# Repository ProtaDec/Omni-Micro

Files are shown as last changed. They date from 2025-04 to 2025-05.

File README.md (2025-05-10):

# Omni-Micro
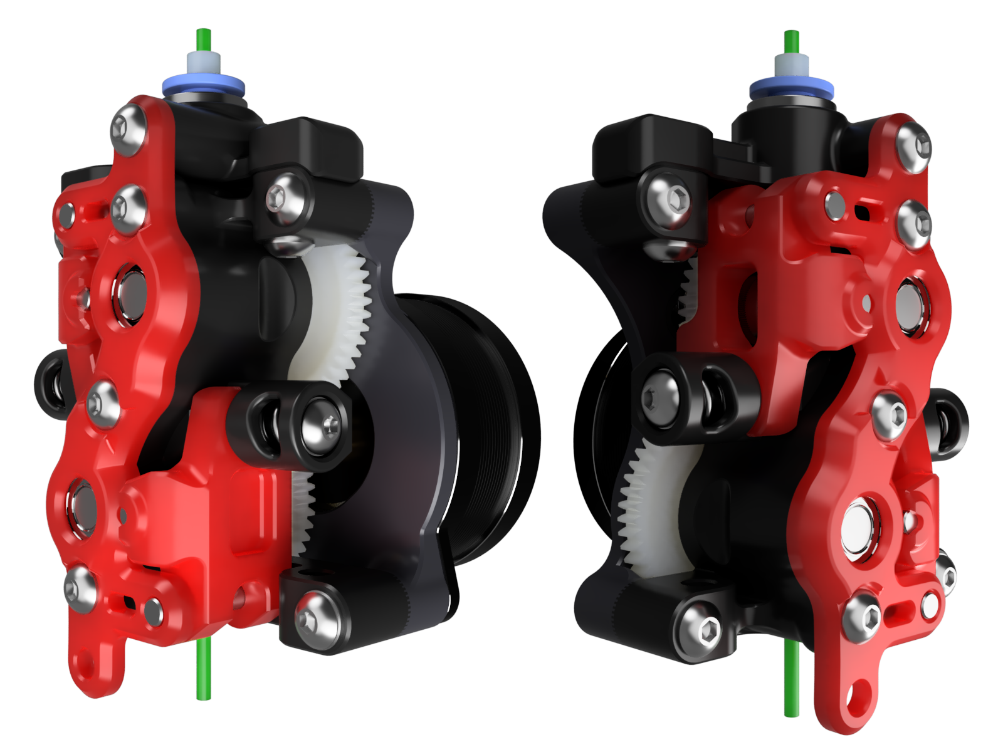
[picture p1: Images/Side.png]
My Image

Double grip modular extruder, based on [Sherpa Micro](https://github.com/Annex-Engineering/Sherpa_Micro-Extruder) by Annex Engineering.
## Concept Features
- Double grip extruders have existed for a while. They help conventional* hotends reach their thermal bottleneck, adding weight and build cost;
- Smooth idler extruders, on the other hand, have proved to increase extruson consistency at the loss of grip;
- I consider this extruder a spiritual successor of the [Sherpa Crew Mini](https://github.com/jrlomas/Sherpa-Crew-Mini) by KR, whom I've been in contact with for a while. I like to think I have improved on the existing formula, while they went for something entirely different, [Mirò](https://github.com/jrlomas/miro-extruder).
  
*Untested with new-generation hotends such as [Chube](https://chubehotend.com/) by Luke's Laboratory.
## Design-specific features
- No alteration of leftover original design elements, except for "fusing" two units;
- Flippable design, compatible with most sherpa micro-friendly toolheads (TBD);
- Four driving configurations & three bowden fitting options;
- Split tensioner with either two regular springs or one cut spring;
- First layer squish compensation built-in (reliability to be confirmed);
- Idler arms and tensioners are compatible with regular Sherpa Micro.
## Future Additions
- Filament sensor;  
  I have an idea of how I want to go about it, but I currently don't own any multi-material DIY printers, and the motivation just isn't there.
- Skeletonized Housing_Rear (maybe).
# BOM
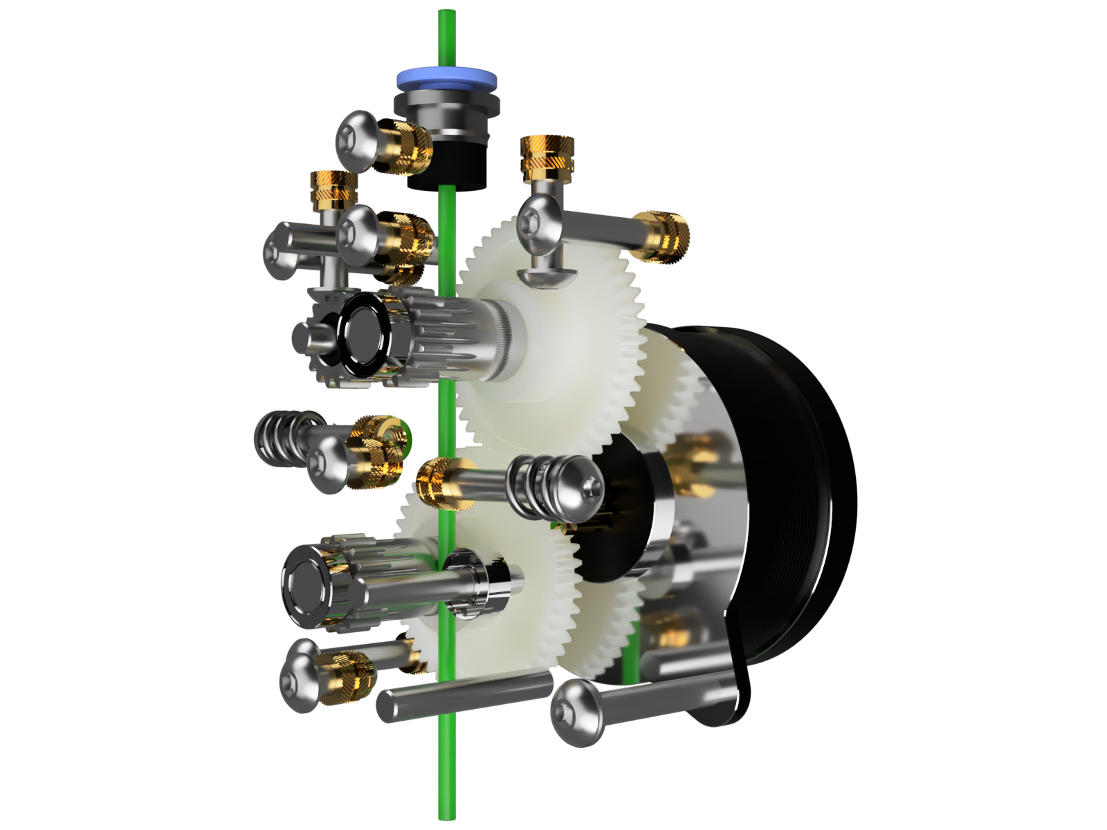
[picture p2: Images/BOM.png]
My Image

## Fasteners

| Article | Qty | Notes |
|---|---|---|
| M3x6(+)mm Ultra Low Profile | 1 | For motor |
| M3x6mm BHCS | 1÷2 | |
| M3x8mm BHCS | 2 | |
| M3x12mm BHCS | 0÷2 | Bowden cap  |
| M3x18mm BHCS | 5 | |
| M3x20(+)mm BHCS | 1 | For motor |
| 3x6x0.2mm Shim | 1 | For motor |
| 3x6x0.5mm Shim | 3 | |
| M3x5x4mm Heat-set Insert | 8÷11 | |

## Extruder Parts

| Article | Qty | Notes |
|---|---|---|
| NEMA14 36mm Stepper 10t to 6t | 1 | |
| BMG Driving Gear Assembly | 2 | OEM RIDGA V2 preferred |
| BMG Idler Gear Assembly | 1÷2 | |
| MR73 Ball bearing | 1÷2 | |
| M3x20 Idler pin | 2÷4 | may need sanding for mr73 |
| Bondtech Spring | 1÷2 | |
| E3D 5mm Collet | 0÷1 | |
| E3D 6mm Collet | 0÷1 | |
| ECAS04 Collet | 0÷1 | |  

# Assembly
Watch the video (https://youtu.be/DaNchYcJ7qc)
### [Watch temporary video here](https://youtu.be/DaNchYcJ7qc)

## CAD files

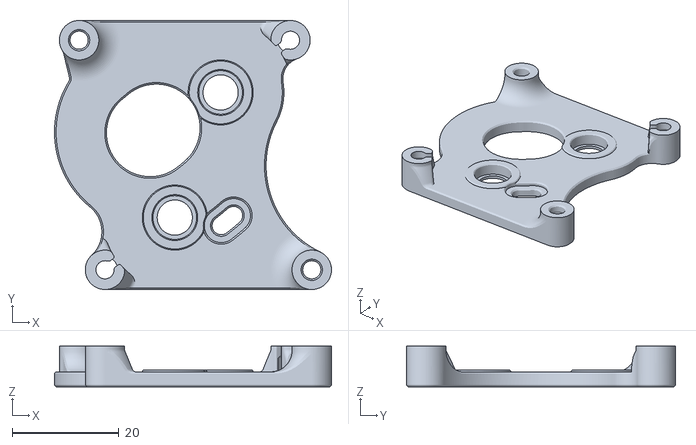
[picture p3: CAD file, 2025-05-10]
STL/(HT)_Housing_Rear_0.2SC_x1.stl
52.0 x 50.5 x 7.60

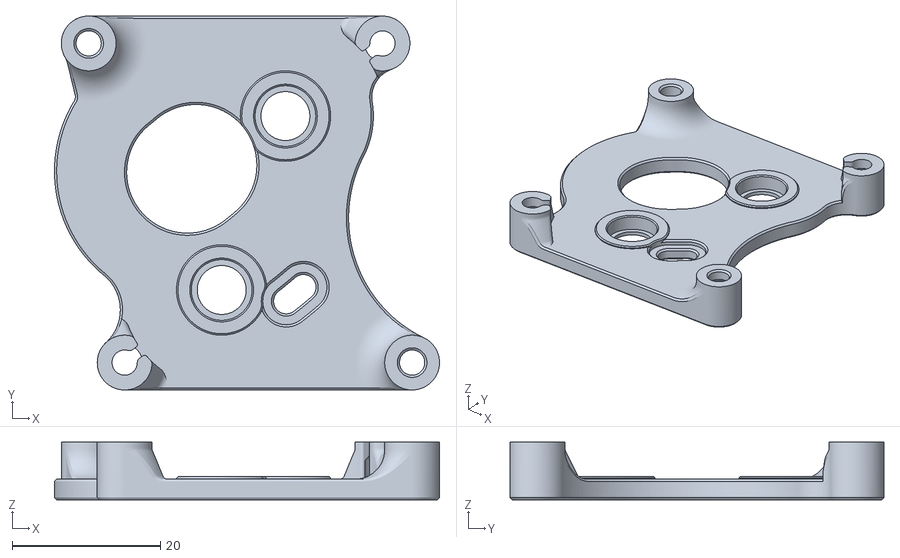
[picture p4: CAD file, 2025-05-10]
STL/(HT)_Housing_Rear_0.4SC_x1.stl
52.0 x 50.5 x 7.80

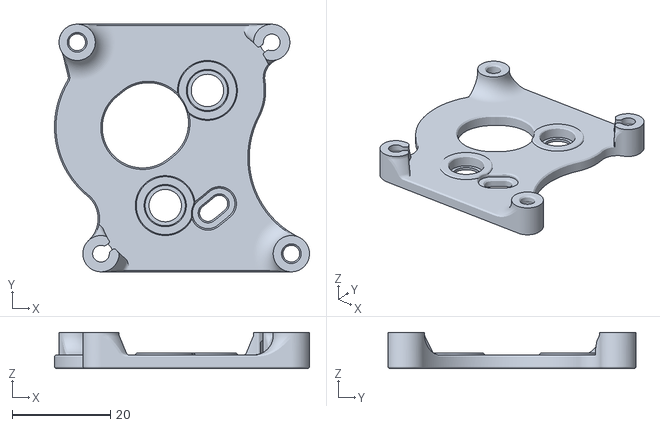
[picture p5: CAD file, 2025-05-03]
STL/(HT)_Housing_Rear_x1.stl
52.0 x 50.5 x 7.40

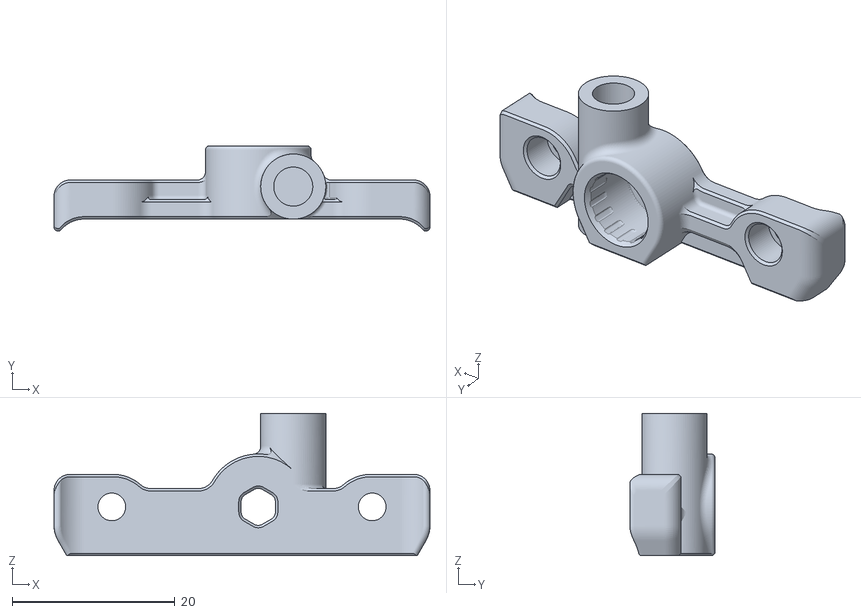
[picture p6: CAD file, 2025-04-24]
STL/Bowden_Cap_ECAS_x1.stl
46.2 x 10.5 x 17.5

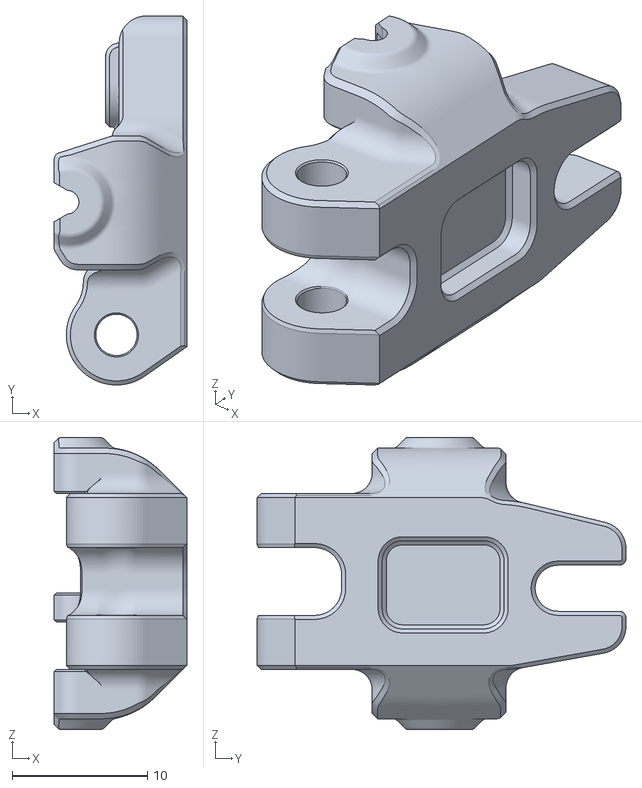
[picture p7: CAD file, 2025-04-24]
STL/(a)_Idler_Smooth_x1.stl
9.80 x 27.3 x 21.6

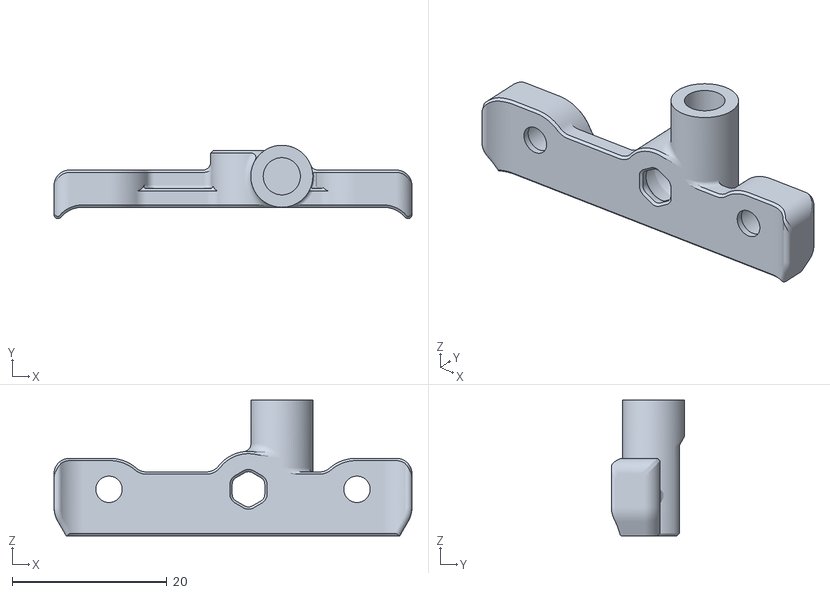
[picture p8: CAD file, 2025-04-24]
STL/Bowden_Cap_5mm_x1.stl
46.2 x 9.48 x 17.5

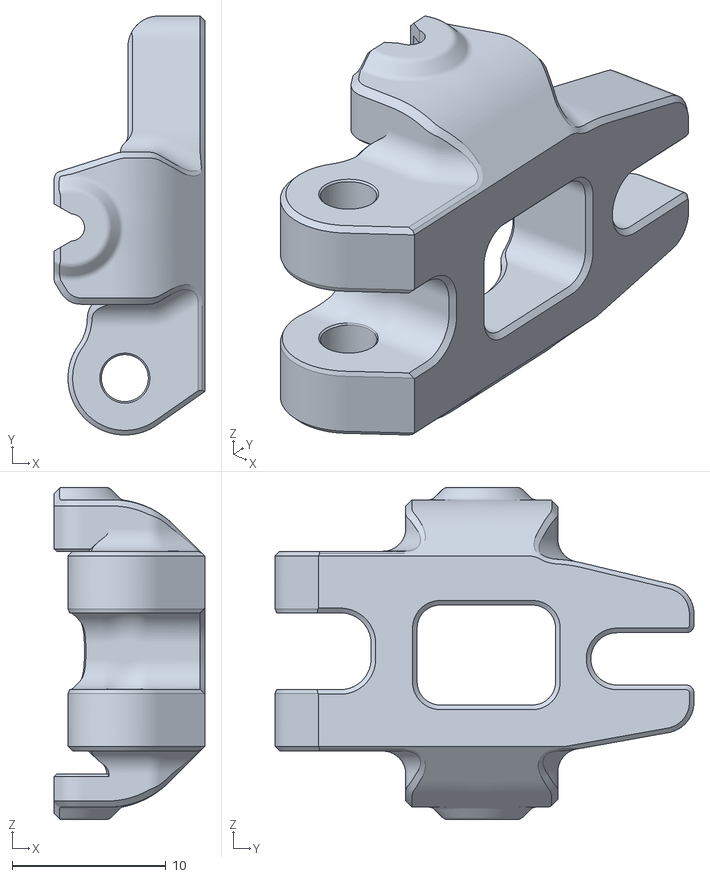
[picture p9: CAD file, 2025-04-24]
STL/(a)_Idler_BMG_x1.stl
9.80 x 27.3 x 21.6

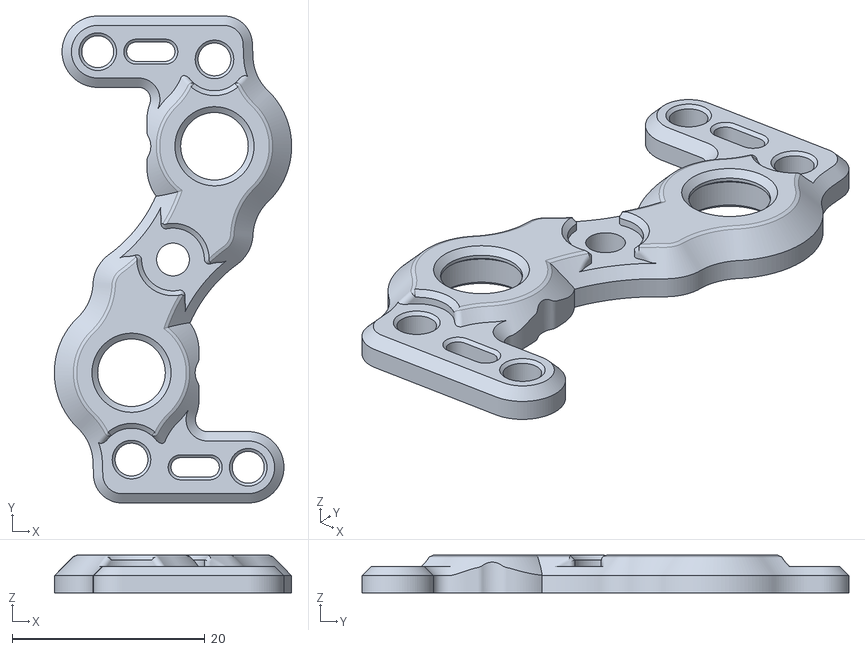
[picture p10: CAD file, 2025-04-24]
STL/(a)_Housing_Front_x1.stl
24.6 x 50.5 x 3.90

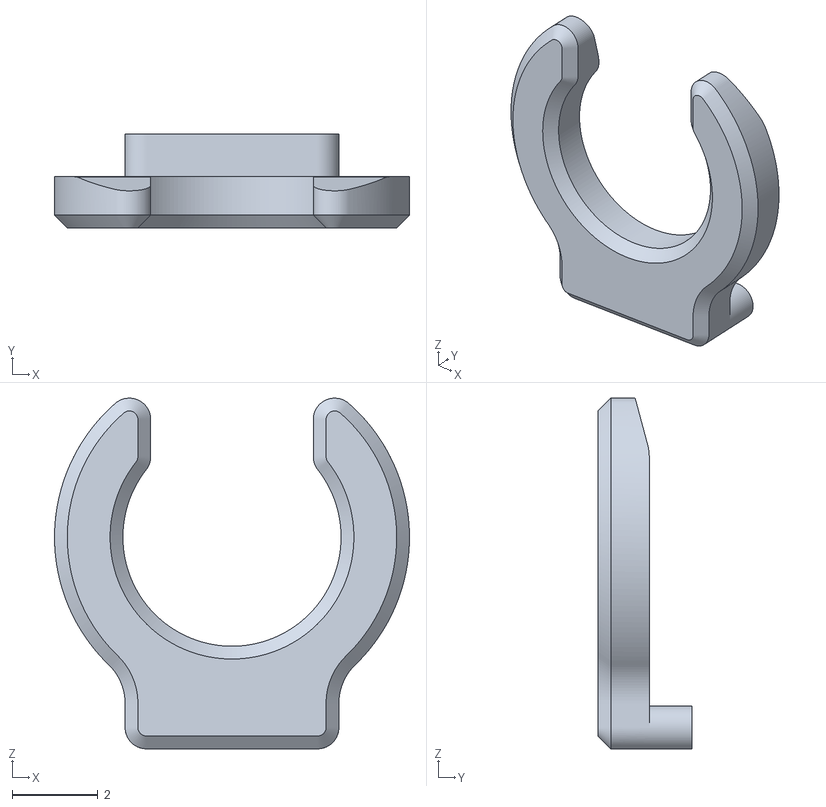
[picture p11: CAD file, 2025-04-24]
STL/(a)_Collet_Clip_5mm.stl
8.30 x 2.20 x 8.20

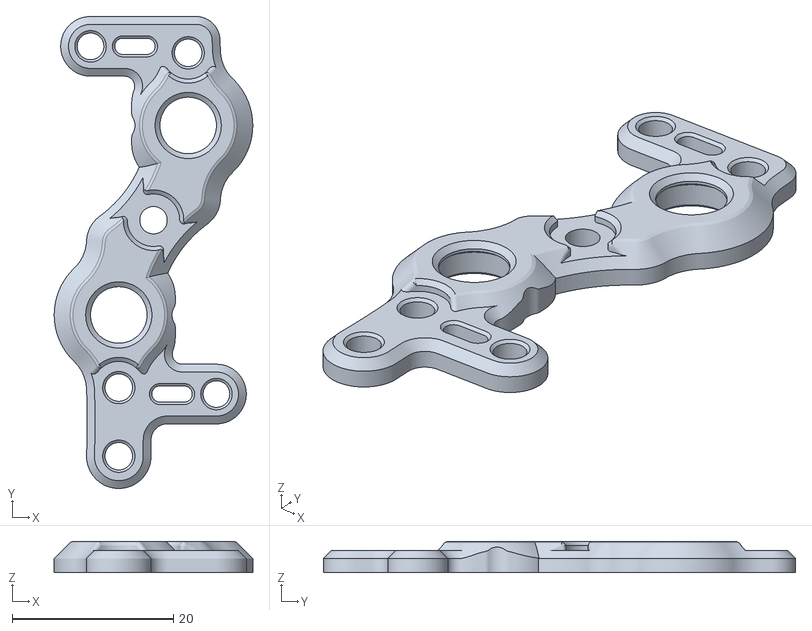
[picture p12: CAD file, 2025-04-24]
STL/(a)_Housing_Front_K_x1.stl
24.6 x 58.5 x 3.90

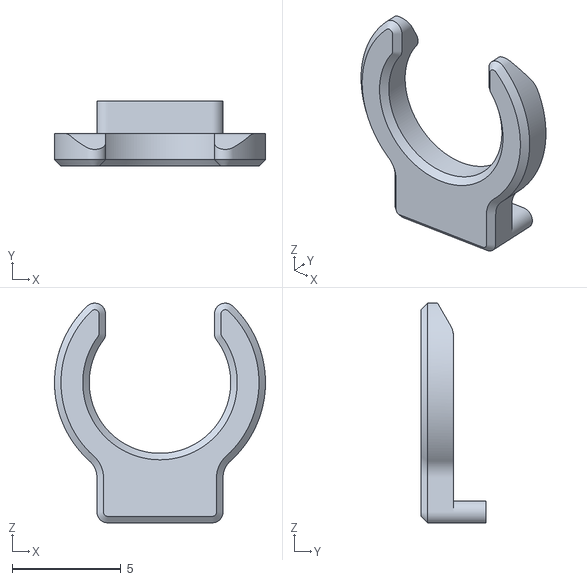
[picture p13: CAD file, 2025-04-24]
STL/(a)_Collet_Clip_6mm.stl
9.70 x 3.00 x 10.1

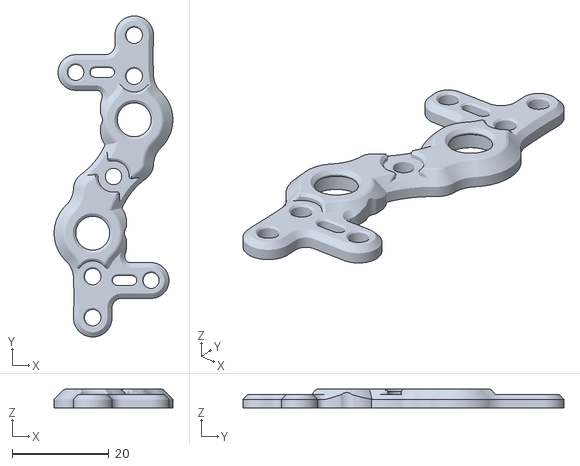
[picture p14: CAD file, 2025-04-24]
STL/(a)_Housing_Front_KK_x1.stl
24.6 x 66.5 x 3.90

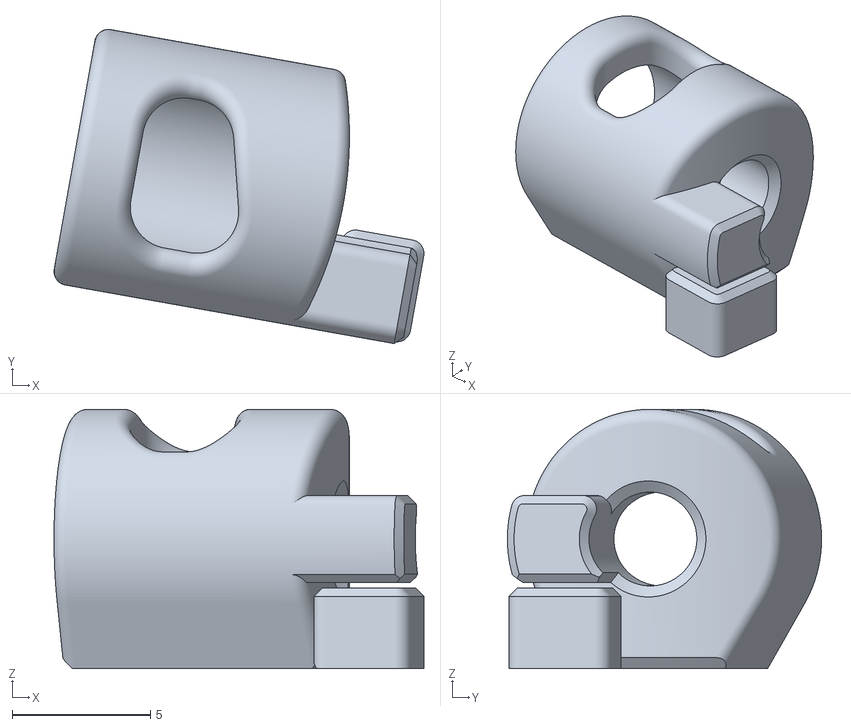
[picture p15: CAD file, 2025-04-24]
STL/Tensioner_Spacer_x2.stl
13.4 x 11.4 x 9.40

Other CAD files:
STL/Bowden_Cap_6mm_x1.stl

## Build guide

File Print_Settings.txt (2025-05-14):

Primary Color: nothing at start of file name
Accent Color: (a)_ at start of file name
High Temp: (HT)_ at start of file name
Quantity Required: _x# near end of file name

Nozzle Size: 0.5mm 
Recommended FDM Materials: ASA
Alternate Approved FDM Materials: PC
Layer Height: 0.25mm
Extrusion Width: Forced 0.5mm
Infill Percentage: 40% minimum (at 0.8mm Width)
Infill Type: Grid, Gyroid, Honeycomb, Triangle or Cubic
Wall Count: 3 minimum (at 0.5mm Width)
Solid Top/Bottom Layers: 4 minimum (at 0.5mm Height)

Nozzle Size: 0.4mm 
Recommended FDM Materials: ASA
Alternate Approved FDM Materials: PC
Layer Height: 0.20mm or 0.25mm
Extrusion Width: Forced 0.4mm
Infill Percentage: 40% minimum (at 0.6mm Width)
Infill Type: Grid, Gyroid, Honeycomb, Triangle or Cubic
Wall Count: 4 minimum (at 0.4mm Width)
Solid Top/Bottom Layers: 4 minimum (at 0.25mm Height)

For Housing_Rear:
Recommended FDM Materials: PC-PBT GF, PET CF, to prevent deformation/melting from motor heat.
Alternate Approved FDM Materials: ABS/ASA if your extruder motor keeps cool enough. More testing needed.
Infill Percentage: 100% at least around the motor mount area.

!!! 0.XSC (Squish Compensation) STLs !!!
Use these if your RIDGA gear's hobbed part does not go far enough towards the motor to align with the filament path.
I have had to use all three variants of Housing_Rear for the corresponding units I made with different filament types.

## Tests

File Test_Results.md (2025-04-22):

# TEST 01
- IDLERS: smooth driving, geared reverse (stock config)
- Filament: Fillamentum Natural PLA @230°C
- Motor: 6T LDO 20mm @0.75a
- Hotend: Dragon Ace Volcano Mini w/100W 24V cartridge
- Nozzle: Panzarnozzle v1 (TC) 0.5mm

| Requested Rate (mm³/s) | Extrusion Rate |
|---|---|
| ≤32 | 100% |
| ≤34 | 99.2% |
| ≤36 | 98.9% |
| ≤38 | 98.5% |
| ≤40 | SKIP |
| **Bottleneck** | *most probably reached max hotend capacity* |

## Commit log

2025-04-24 STLs added
    [(a)_Collet_Clip_5mm.stl, (a)_Collet_Clip_6mm.stl, (a)_Housing_Front_KK_x1.stl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]
2025-04-25 Logo printability
    [Housing_Rear_x1.stl]
2025-05-03 New rear hosuing stls
    [(HT)_Housing_Rear_0.2SC_x1.stl, (HT)_Housing_Rear_0.4SC_x1.stl, (HT)_Housing_Rear_x1.stl]
2025-05-10 Updated STLs
    - Removed old indicators;
    - Clearer indicator for housing core;
    - Added text on squish compensation housing rear STLs.
    [(HT)_Housing_Rear_0.2SC_x1.stl, (HT)_Housing_Rear_0.4SC_x1.stl]
2025-05-10 Update README.md
    Minor BOM fix
